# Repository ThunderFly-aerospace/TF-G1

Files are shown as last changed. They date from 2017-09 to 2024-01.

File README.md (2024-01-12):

# TF-G1 - Unmanned Autogyro Extreme weather sensor carrier  

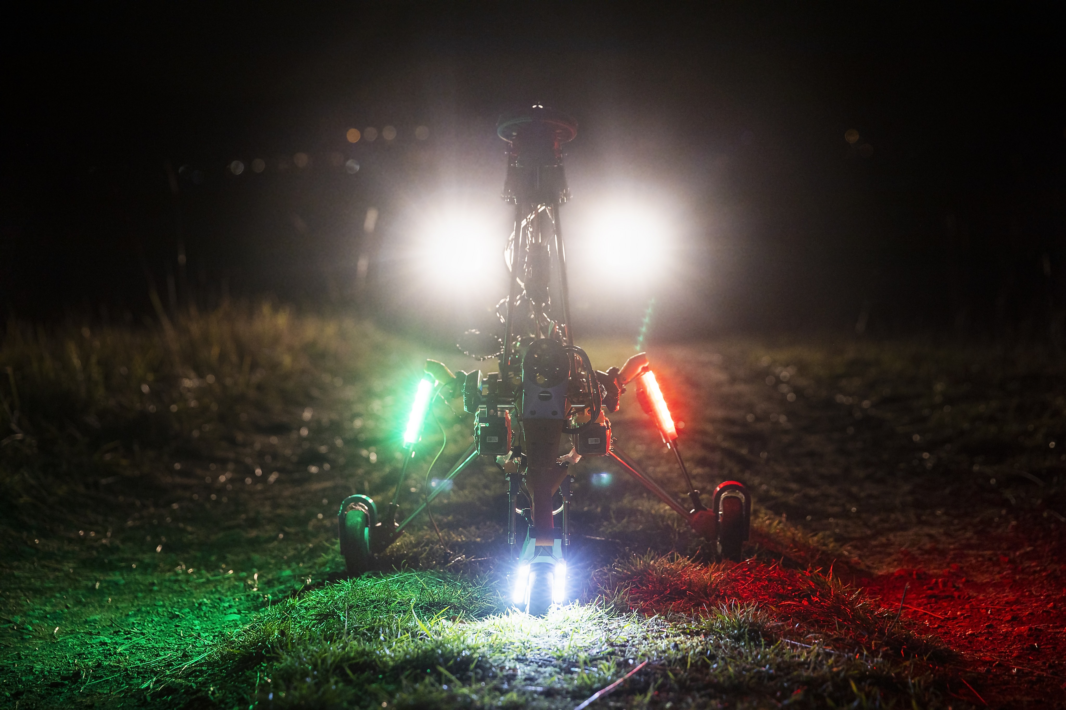
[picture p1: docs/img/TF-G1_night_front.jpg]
TF-G1 front view in night


The TF-G1 autogyro created by ThunderFly s.r.o. is a [unmanned aerial vehicle (UAV)](https://en.wikipedia.org/wiki/Unmanned_aerial_vehicle) designed to be operable in almost any weather.
The main features of that design are:

  * Payload capacity of a few kilograms
  * Weather-insensitive operation
  * Low audible noise
  * High safety due to stable autorotation mode which does not require autopilot or pilot attention
  * Greater altitude and area coverage than existing UAV designs  like multi-copters or helicopters
  * High maneuverability and agility
  * Absence of [downwash](https://en.wikipedia.org/wiki/Downwash), therefore a minimal occurrence of [Brownout](https://en.wikipedia.org/wiki/Brownout_(aeronautics))
  * High descent rates
  * [Simulation model available](https://github.com/ThunderFly-aerospace/FlightGear-TF-G1)
  * Easily repairable and maintain
  * Exceptional flight tolerance to rotor blade damage
  * Car roof takeoff ready

The benefits that come from this feature set are the usability of applications where the system could be potentially damaged, although the safety must remain as high as possible.  An example of this application is searching and rescue missions in harsh weather unflyable by conventional aircraft. For additional information contact ThunderFly s.r.o. representative at info@thunderfly.cz

## Why autogyro? 

Autogyro

In contrast to the well-known [VTOL](https://en.wikipedia.org/wiki/VTOL) aircraft designs. The autogyro could be considered a short take-off and vertical landing aircraft ([STOVL](https://en.wikipedia.org/wiki/STOVL)). Therefore it is suitable for a wide range of different applications. The main advantages to other well-known airframes: 

* Ability to take off and land using a short runway (almost zero length).
* High resistance to weather conditions, especially gusts of wind or thermals.
* An unpowered rotor enables it to operate in an autorotation mode (one of the helicopter’s emergency modes). Consequently, it does not need to actively change a flight mode in case of failure (it does not need a parachute or other actively working devices). Its flight is thus inherently stable and safe at all times.
* Autogyro has significantly reduced audible noise due to the slowly rotating rotor and propeller. 
* Absence of a downwash - during take-off or landing the creation of an unwanted swirling of dust is eliminated.
* Low lift-to-drag ratio that can be adjusted by construction parameters. This ability can be useful because an unmanned autogyro cannot fly very far in the case of control failure (as is the case of a conventional airplane), the flight is still safe and the autogyro cannot fall (as is typical for multi-copters or wrongly piloted helicopters).

The autogyro has generally many construction variants. The one, which is in the scope of this repository has a fully tilted rotor. The main advantage of this construction feature is obtaining better controllability over its wide airspeed range. It can also be controlled down to zero forward airspeeds, compared to a classical rudder/elevator setup.

## Repository content

This repository contains open-source design files of the autogyro construction. Most components are 3D-printed. However, the printable data (gcodes) are generated by our special software suite - processor3D. It is required that parts are sliced properly according to the material to make sure that resulted in 3D-printed parts can be used safely for the flight. **Therefore for safety reasons we do not recommend attempting to slice the parts yourself. It is better to contact us.**

The product, support, or accessories could be obtained from [ThunderFly s.r.o.](https://www.thunderfly.cz/), via an email to info@thunderfly.cz . 

### Contribution

In case you want to contribute to the open-source project we have a [contribution guideline](https://github.com/ThunderFly-aerospace/TF-G2/blob/4s/CONTRIBUTING.md). Your contribution is very welcome! For a contribution, you can get access to the optimized and safe printable files (gcodes).

##### Build

Most of the components are coded in OpenSCAD. To render all components run the following commands in Linux CLI:

    sudo pip install stlsort

    sudo apt install python3-numpy-stl

    make

The design files and related documents are covered by [GNU GENERAL PUBLIC LICENSE Version 3](https://www.gnu.org/licenses/gpl-3.0.en.html)

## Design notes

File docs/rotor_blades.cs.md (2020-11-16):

## Rotorové listy pro vírník TF-G1

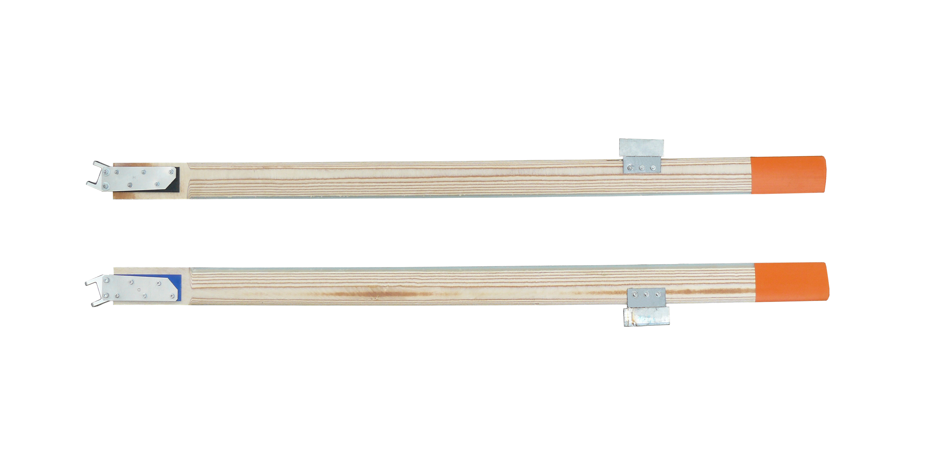
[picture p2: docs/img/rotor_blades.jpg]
Pár rotorových listů pro TF-G1


Rotorové listy vírníku TF-G1 jsou vícevrstvé z dřevo-skelného kompozitu. Každý list je pečlivě CNC frézován ve dvojici s druhým rotorovým listem pro udržení  precizního vyvážení každého rotorového páru.

Konstrukce listu je založena na sendvičové konstrukci, kde vnitřní stringer je dimenzován pro maximální únosnost 4kN, což odpovídá maximálním otáčkám 1500 ot/minutu.  Všechny vrstvy sendviče jsou vakuově lisovány pro eliminaci vzniku bublinek ve vnitřních lepených spojích.
Listy jsou vytvrzeny v autoklávu a povrchově ošetřeny epoxidovým lakem.

Závěs rotorového listu je navržen pro využití na Delta-3 rotorové hlavě s kluznými ložisky a broušeným ocelovým čepem 4H9.

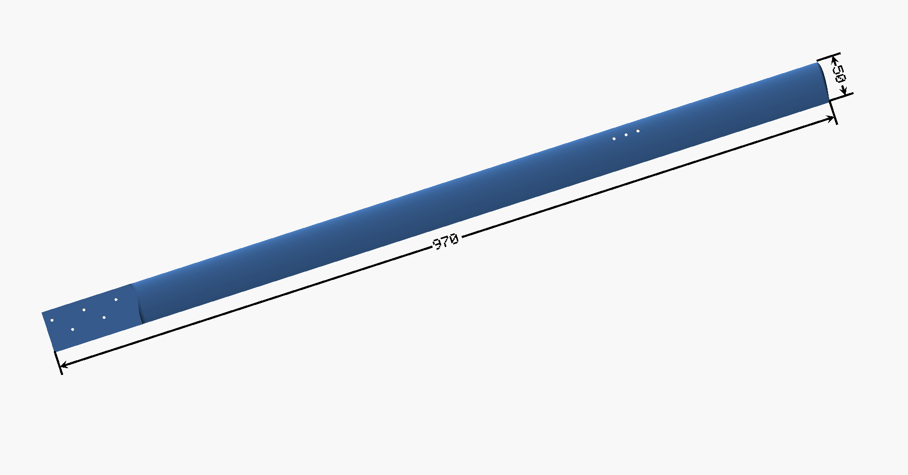
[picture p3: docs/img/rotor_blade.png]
TF-G1 samostatný rotorový list


Hlavní parametry rotorových listů

  - Aerodynamický profil NACA0016
  - Aerodynamické křížení: žádné
  - Průmět - obdélníkový
  - Hloubka listu 50mm
  - Délka 970mm
  - Maximální otáčky - 1500
  - Materiál: březový kompozit v kombinaci se skelnými vlákny FR4.
  - Hmotnost 564g
  - Typ kování: Pro Delta-3 rotorovou hlavu

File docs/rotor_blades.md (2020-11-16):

## TF-G1 Rotor Blades

Pair of TF-G1 rotor blades

TF-G1 rotor blades are multilayer wood-composite autogyro rotor blades.  The each blade is carefully CNC machined in tandem with the second rotor blade to maintain precise balance of each rotor pair.
The blade construction is based on wood-fiber-wood sendwitch, where internal stringer core is dimensioned to windstand 4kN centrifugal force corresponding to 1500 RPM.
Rotor blades has delta-3 rotor head mount.

TF-G1 plain rotor blade

Main blade parameters

  - Blade airfoil NACA0016
  - Shape - rectangle
  - Depth 50mm
  - Lenght 970mm
  - Maximal RPM - 1500
  - Material - birch plywood, glass fiber composite
  - Mass 564g
  - Blade mount type: Delta-3 rotor head

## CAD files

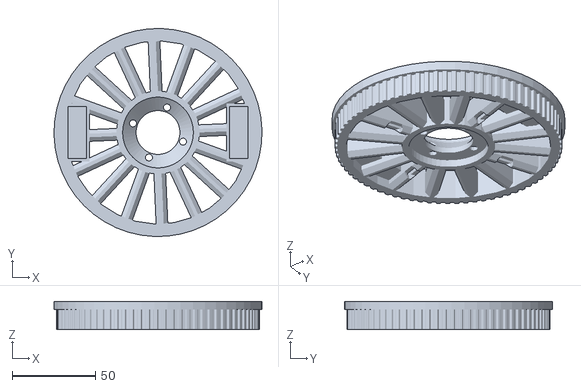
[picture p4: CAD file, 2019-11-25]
STL/drawings/assembly_head_rotor_printed.stl
125.0 x 124.9 x 17.0

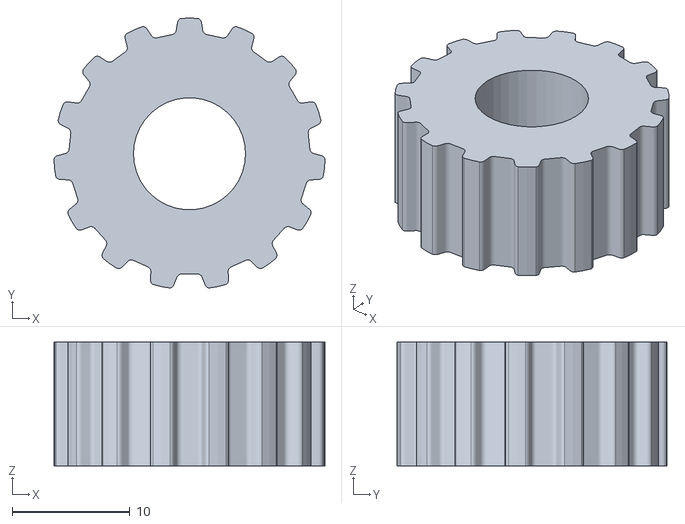
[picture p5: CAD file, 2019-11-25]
STL/drawings/assembly_printed_head_pulley_motor.stl
23.0 x 22.9 x 10.5

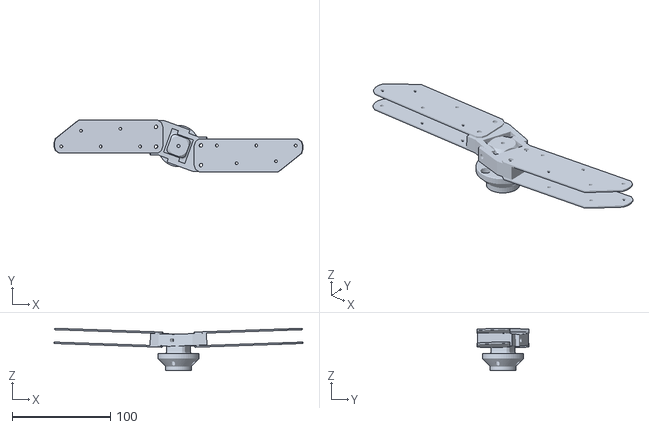
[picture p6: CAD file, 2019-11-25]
STL/drawings/assembly_head_rotor_alu.stl
252.9 x 52.3 x 43.1

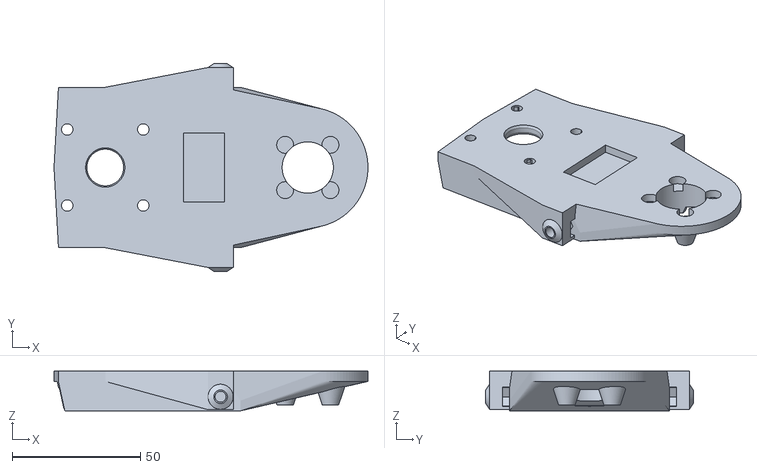
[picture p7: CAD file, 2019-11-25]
STL/drawings/assembly_head_plate_printed.stl
122.5 x 81.0 x 15.5

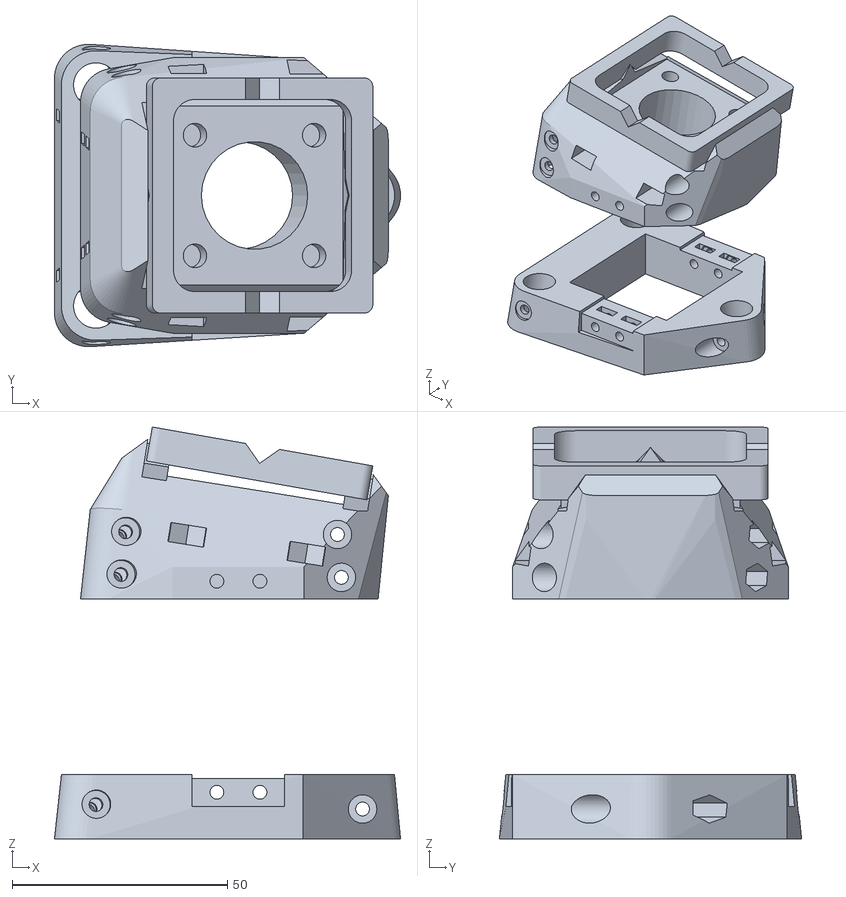
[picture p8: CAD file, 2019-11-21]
STL/drawings/assembly_printed_head.stl
80.4 x 70.2 x 95.7

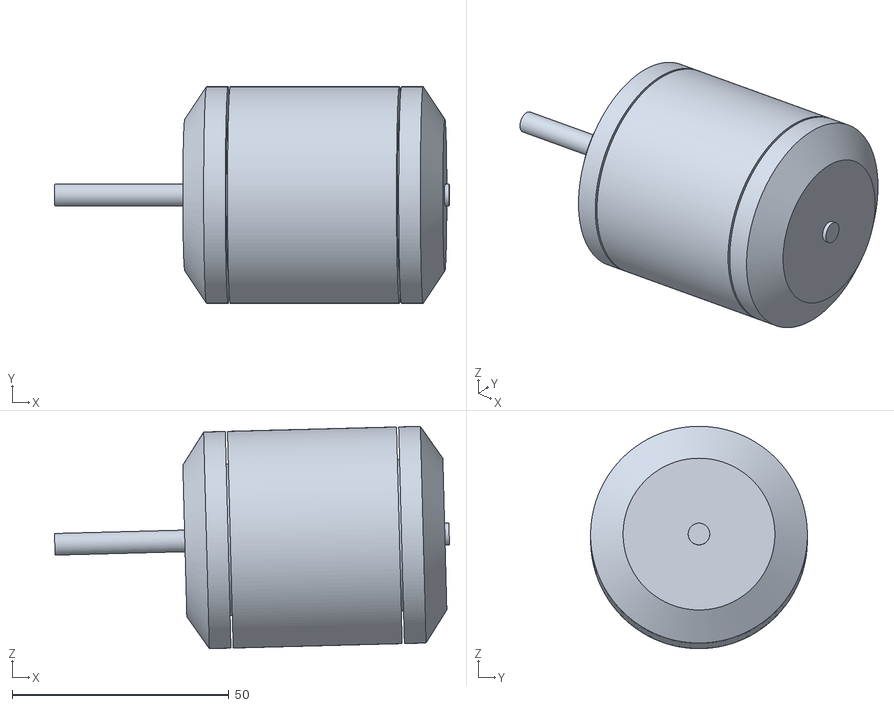
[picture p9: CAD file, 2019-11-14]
STL/main_motor.stl
91.1 x 50.0 x 51.3

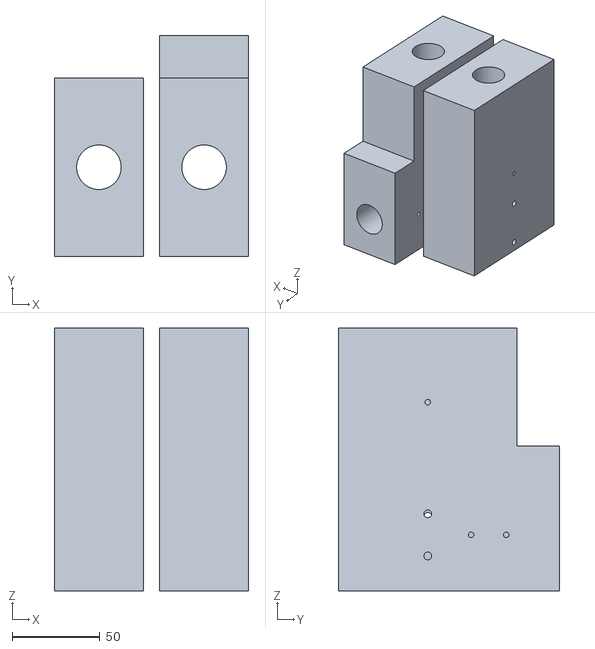
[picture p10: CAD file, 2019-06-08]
STL/manufacturing_helpers/print_plate_1014main_tube.stl
110.8 x 125.8 x 150.0

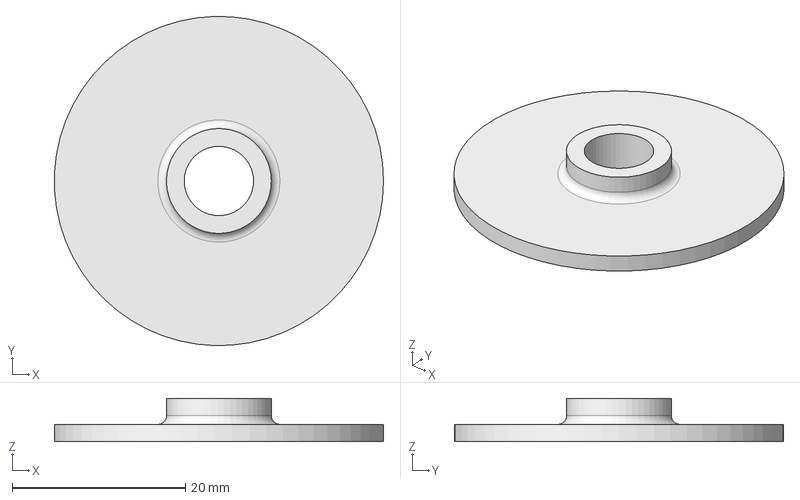
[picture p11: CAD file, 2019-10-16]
src/666_1264.FCStd
38.0 x 38.0 x 5.00 mm

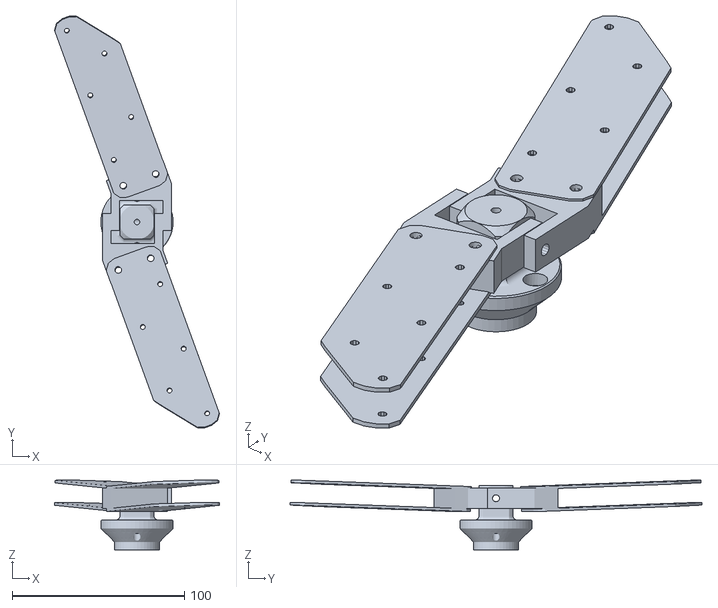
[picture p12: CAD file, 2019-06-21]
src/drawings/visual_model/rotor_hinges.stl
95.9 x 239.4 x 40.6

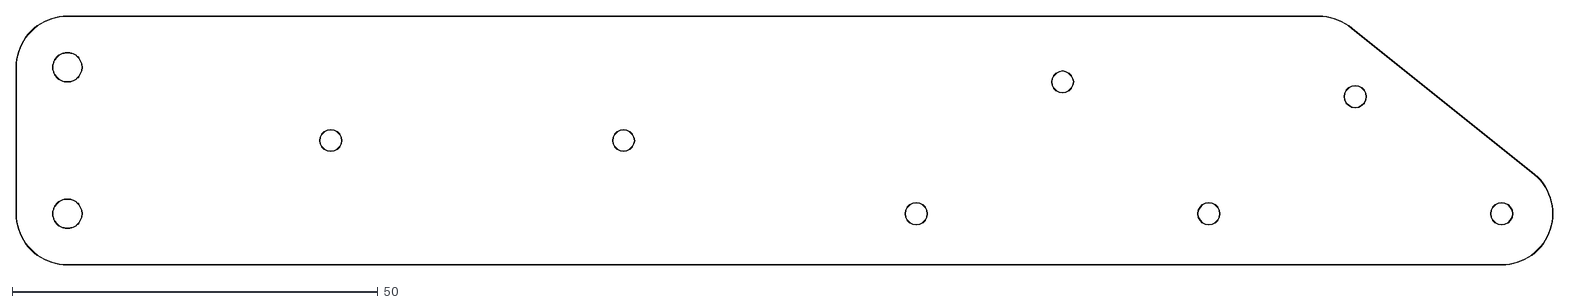
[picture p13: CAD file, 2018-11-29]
src/milling/DXF/666_1050_projection.dxf
210.0 x 34.0

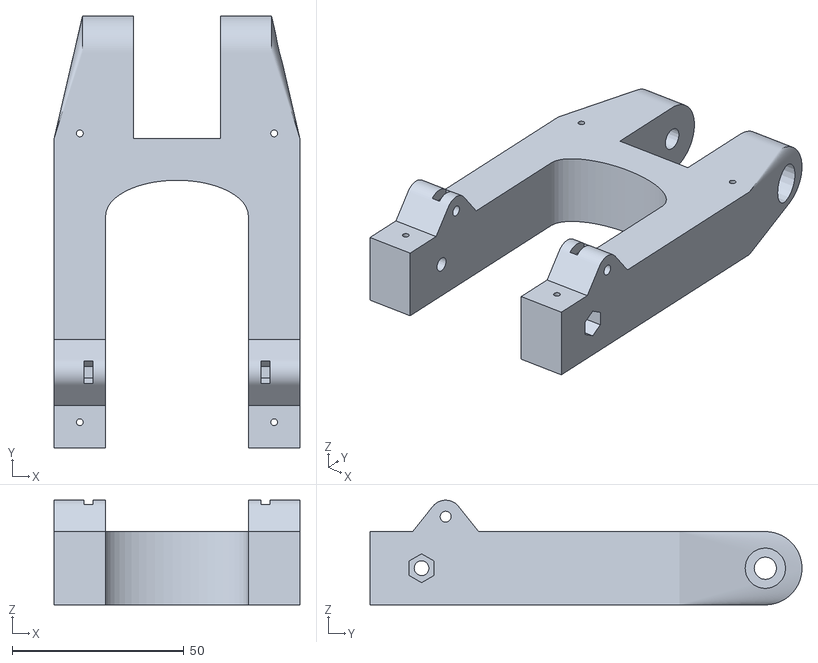
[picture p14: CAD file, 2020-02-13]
STL/888_2022.stl
71.5 x 125.7 x 30.5

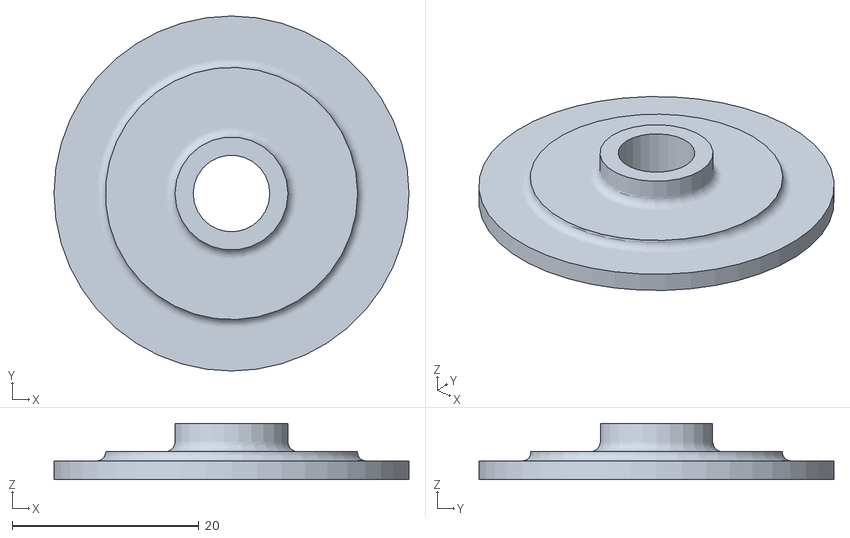
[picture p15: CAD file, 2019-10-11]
STL/manufacturing_helpers/666_1264_print.stl
38.0 x 38.0 x 6.00

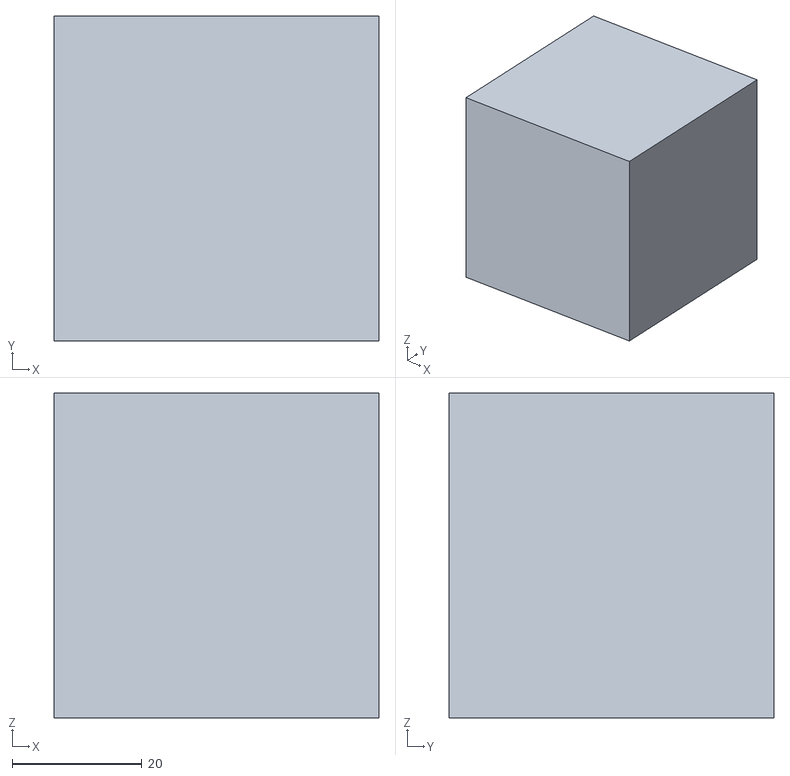
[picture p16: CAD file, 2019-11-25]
STL/testing/cube_center.stl
50.0 x 50.0 x 50.0

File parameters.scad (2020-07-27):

use <src/lib/vector.scad>

global_clearance = 0.5;
perimeter = 0.41;
layer = 0.2;
week = "77"; // Popisek s cislem tydne, nastavuje se z makefilu

// obecne rozmery trubek
carbon_pipe_10_outer_diameter = 10.4;
carbon_pipe_10_inner_diameter = 6;

//Main tube diameter - hole [mm]
main_tube_outer_diameter = 25.4;
main_tube_inner_diameter = 23.05;

//Tube for undercarriage - rendered hole [mm]
tube_for_undercarriage_outer_diameter = carbon_pipe_10_outer_diameter;
tube_for_undercarriage_inner_diameter = carbon_pipe_10_inner_diameter;

//Tube for pilon - rendered hole [mm]
pilon_pipe_diameter = carbon_pipe_10_outer_diameter;
pilon_pipe_diameter_inner = carbon_pipe_10_inner_diameter;


// Parametry hlavniho nosniku

beam_vertical_space_between_pipes = 1;
beam_min_wall = 3;
beam_socket_width = 25;

// tloustka limce
ring_thickness = 2*10 + beam_vertical_space_between_pipes + 3*beam_min_wall;

// tloustka podlozky, a tloustka podlozky od stredu smerem nahoru/dolu
beam_thickness = 2*10 + beam_vertical_space_between_pipes + 2*beam_min_wall;
beam_thickness_above = 5 + beam_min_wall;
beam_thickness_below = 5+ beam_vertical_space_between_pipes + 10 + beam_min_wall;
//beam_thickness = 30;
beam_width = 80;
beam_length = 490;
beam_edge_angle = 60/2;
beam_division = [0, 145, 275, 417, 1000];

beam_main_pipe_diameter = carbon_pipe_10_outer_diameter;
beam_main_pipe_distance = 45;
beam_main_pipe_thickness = carbon_pipe_10_outer_diameter;

beam_patern = 40;
beam_side_edge_width = 175;

// Parametry pro limec

collar_holes_distance = 200; // Vzdalenost der pro sesroubovani pricnych tyci. Vzdalenost na trubce
beam_side_pipe_distance = collar_holes_distance; // TODO: odstranit tento parametr


// Nastavení parametrů rotoru

gliding_aggle = 14;         // tenhle úhel by se zřejmě v budoucnu měl počítat z požadované klouzavosti.

rotor_blade_AOA = 3;      // nastavení úhlu náběhu rotorového listu
rotor_blade_length = 970;   // délka rotorového listu
rotor_blade_depth = 50;     // hloubka rotorového listu
rotor_flap0 = 2;
rotor_delta = 20;

/* // parametry rotorove hlavy

rotor_head_pitch = 0;
rotor_head_roll = 0;

rotor_head_height = 78; // vzdalenost spodni zakladny rotorove hlavy od stredu kuloveho loziska
rotor_head_width = 70; // je to "sirka" v ose X
rotor_head_rank_angle = 9; // zakloneni rotorove hlavy pri nulove vychylce.
rotor_head_bearing_x_shift = -0; // posun kuloveho loziska dopredu dozadu.
*/

rotor_head_plate_bearing_center_distance = 14;     // vzdalenost horni spodni steny placky od stredu loziska
rotor_head_limiter_above = 12; // jak moc vysoko ma byt divnotvar nad stredem loziska
rotor_head_limiter_below = 3; // jak moc nizko ma byt divnostvar pod stredem loziska

// nastavení parametrů motoru

engine_angle = -1.5;
engine_diameter = 55;
engine_offset = 65;
engine_holder_beam_depth = 50; // jak moc je nosnik zapusten v dilu

engine_screws_radius = 15;
engine_holes_radius = (24 + 44)/4;
engine_shatf_hole_diameter = 13;

// Parameters of tube couplings
coupling_wall_thickness = main_tube_outer_diameter/5;  //width of coupling walls
thickness_between_tubes = main_tube_outer_diameter/10;    // minimum distance between tubes in couplings

coupling_wall_thickness_undercarriage = tube_for_undercarriage_outer_diameter/3;
thickness_between_tubes_undercarriage = tube_for_undercarriage_outer_diameter/10;

608_bearing_outer_diameter = 22.3;
608_bearing_inner_diameter = 8-0.3+0.4;
608_bearing_thickness = 7.1;

696_bearing_outer_diameter = 15.3;
696_bearing_inner_diameter = 6-0.3+0.4;
696_bearing_thickness = 5.1;

//parametry mechoveho kola
wheel_inner_diameter = 36;
wheel_inner_thickness = 28;
wheel_outer_diameter = 108;

wheel_disc_diameter = 51;
wheel_disc_upper_thickness = 5;
wheel_disc_upper_difference = 7;

// screw length step - minimum difference in length between two types of screws
basic_screw_length = 5;

//Square nut for M6 [mm]
M6_square_nut_length = 10;
M6_square_nut_height = 3.2;

//Screw diameter and nut for M10 [mm]
M10_screw_diameter=10.4;
M10_head_height = 10;
M10_head_diameter = 16+0.5;
M10_nut_height = 10.5;
M10_nut_diameter = 25.5;
M10_nut_pocket = 22.3;

//Screw diameter for M8 [mm]
M8_screw_diameter = 8 + 0.5;
M8_head_height = 8;
M8_head_diameter = 13.5;
M8_nut_height = 7.5;
M8_nut_diameter = 14.4 + 0.5;
M8_nut_pocket = 13 + 0.5;

M8_plug_diameter = 8;

//Screw diameter and nut for M6 [mm]
M6_screw_diameter=6.5;
M6_head_diameter = 10+0.5;
M6_head_height = 6;
M6_nut_height = 4.9;
M6_nut_diameter = 11.8;
M6_nut_pocket = 10.4;

//Screw diameter and nut for M5 [mm]
M5_screw_diameter=5.5;
M5_head_height = 5;
M5_head_diameter = 13+0.5;
M5_nut_height = 4 + 0.5;
M5_nut_diameter = 9.4;
M5_nut_pocket = 8.4;

//Screw diameter and nut for M4 [mm]
M4_screw_diameter=4.3;
M4_screw_head_height = 4.5;
M4_nut_height = 3.2 + 0.5;
M4_nut_diameter = 8.4;
M4_nut_pocket = 7.5;

//Screw diameter and nut for M3 [mm]
M3_screw_diameter = 3.2;
M3_nut_height = 2.7;
M3_nut_diameter = 6.6;
M3_screw_head_height = 3;
M3_nut_pocket = 5.6;

//Screw diameter and nut for M2,5 [mm]
M2_5_screw_diameter = 2.7;
M2_5_nut_height = 2.3;
M2_5_nut_diameter = 6;
M2_5_nut_pocket = 5.1;

//Screw diameter and nut for M2 [mm]
M2_screw_diameter = 2.1;
M2_nut_height = 2;
M2_nut_diameter = 4.5;
M2_nut_pocket = 3.95;

//M3 ISO7380
M3_ISO7380_head_height = 1.5;
M3_ISO7380_nut_height = 3;
M3_ISO7380_nut_diameter = 5.7+0.5;

//sroub servo
Servo_screw = 1.5;
Servo_nut_height = 1;
Servo_nut_diameter = 2.7;

//The tube for help
Help_main_tube_outer = 25;
Help_main_tube_inner = 23;
Help_tube_for_undercarriage_outer = 10;
Help_tube_for_undercarriage_inner = 5;


//main hull parameters

hull_drop_length = 720;  // zajím sjednoceno s hull_x_size, ale v budoucnu by tento parametr chtělo zrušit
hull_wall_thickness = 0.8;
hull_y_size = 150;
hull_z_size = 230;
hull_x_size = hull_drop_length;
hull_corner_radius = 4;
hull_airfoil_thickness= 0035;  // thickness of drop generating airfoil in percent of length.
hull_scale_x = 1;
hull_scale_y = 1.5;
hull_scale_z = 1.5;

hull_strenghtening_pipe_distance = 45;




// Parametry pylonu k rotorove hlave

main_pilon_position = 170+68+beam_patern;       // pozice rotorového pilonu měřená od přední části krytu

// vzdalenosti jsou pocitany od stredu rotoru
// vzdalenosti jednotlivych tyci u podlozky
//pilon_pipe_base_front_x = 30;
pilon_pipe_base_front_x = +engine_holder_beam_depth + main_pilon_position - beam_patern*6.75;
pilon_pipe_base_front_y = 55;
pilon_pipe_base_front_z = 0;

pilon_pipe_base_rear_x = -engine_holder_beam_depth + beam_patern*9.75 - main_pilon_position;
pilon_pipe_base_rear_z = beam_thickness_above;

// vzhalenosti jednotlivych tyci u rotorove hlavy
pilon_pipe_head_front_x = 20;
pilon_pipe_head_front_y = 20;
pilon_pipe_head_rear_x = 30;

cover_pilon_position = main_pilon_position - 42;
cover_pilon_naca = 0060;
height_of_vertical_tube = 350; //278mm je změřená délka trubky.



//délka hlavní dlouhé trubky
length_of_main_tube = 820;
length_of_undercarriage_tube_front = 150;
length_of_undercarriage_tube_rear = 320; //500;

ribbon_width = 5; // šířka vyztužovacích lemů.

// šířka otvoru v přední části kapoty pro držák motoru.
width_of_engine_holder = 83;

//Top Cover Division - dělení horního krytu pro tisk
top_cover_division = [0, 50, 150, 290, 435, 580, hull_x_size];
top_cover_strip_zposition = 0;
//Bottom Cover Division - dělení dolního krytu pro tisk
bottom_cover_division = [0,145,290,365, 470, hull_x_size];
bottom_cover_strip_zposition = -15;
// zkrácená část pro payload pro testovací tisk
//bottom_cover_division = [0,200,250,365, 470, hull_x_size];


rotor_height = height_of_vertical_tube + main_tube_outer_diameter/2 + 2*global_clearance + thickness_between_tubes + 30; // změřená výška rotoru je 367mm
center_of_gravity_position = [main_pilon_position - tan(gliding_aggle)*rotor_height, 0, 0];


//Cover pilon division - na výšku (v ose Z)
cover_pilon_division = [0,170,height_of_vertical_tube + main_tube_outer_diameter + coupling_wall_thickness];
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

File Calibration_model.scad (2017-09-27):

include <./Parameters.scad>
wall_thickness = main_tube_outer_diameter/5;
width = wall_thickness * 3 + main_tube_outer_diameter + main_tube_inner_diameter;
depth = main_tube_outer_diameter + wall_thickness * 2;
height = 20;
protrusion_height = 10;

difference () {

translate ([-(main_tube_outer_diameter/2+wall_thickness),-(main_tube_outer_diameter/2+wall_thickness),0])
cube ([width,depth,height]);

cylinder (h = height, r1 = main_tube_outer_diameter/2, r2 = main_tube_outer_diameter/2);

translate ([-main_tube_outer_diameter/2,-main_tube_outer_diameter/2,0])
cylinder (h = height, r1 = M4_screw_diameter/2, r2 = M4_screw_diameter/2);

translate ([main_tube_outer_diameter/2 + wall_thickness + main_tube_inner_diameter/2,-4,0])
cylinder (h = height, r1 = tube_for_undercarriage_outer_diameter/2, r2 = tube_for_undercarriage_outer_diameter/2);

}

union () {

	difference(){

	translate ([main_tube_outer_diameter/2 + wall_thickness + main_tube_inner_diameter/2,-4,-(protrusion_height)])
	cylinder (h = protrusion_height, r1 = main_tube_inner_diameter/2, r2 = main_tube_inner_diameter/2);

		translate ([main_tube_outer_diameter/2 + wall_thickness + main_tube_inner_diameter/2,-4,-protrusion_height])
		cylinder (h = protrusion_height, r1 = tube_for_undercarriage_outer_diameter/2, r2 = tube_for_undercarriage_outer_diameter/2);


}
}

union(){

	translate ([main_tube_outer_diameter/2 + wall_thickness/2+2,main_tube_outer_diameter/2 - 2,-protrusion_height])
	cylinder (h = protrusion_height, r1 = tube_for_undercarriage_inner_diameter, r2 = tube_for_undercarriage_inner_diameter);

}

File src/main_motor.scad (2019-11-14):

include <../parameters.scad>
use <lib/motor.scad>

module position_main_motor(){
		translate([-engine_offset*2.2, 0, engine_offset])
		rotate([0, 90+engine_angle, 0])
		children();
}

position_main_motor()
motor_main();

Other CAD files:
STL/assembly_head_plate_printed.stl
AMF/4printing/print_plate_888_1025B1.stl
AMF/888_1038.stl
STL/blades/printplate_888_4101_printtest.3mf
src/motor_imitation.scad
666 1017_promenne.scad
666_1004.scad
666_1004_promenne_final_1.scad
666_1014.scad
666_1017.scad
666_1019.scad
AMF/333_1037.amf
AMF/4printing/print_plate_1014.amf
AMF/4printing/print_plate_1014.stl
AMF/4printing/print_plate_1019A.amf
AMF/4printing/print_plate_1019A.stl
AMF/4printing/print_plate_1019B.amf
AMF/4printing/print_plate_1019B.stl
AMF/4printing/print_plate_1020.amf
AMF/4printing/print_plate_1020.stl
AMF/4printing/print_plate_1024A.amf
AMF/4printing/print_plate_1024A.stl
AMF/4printing/print_plate_1024B.amf
AMF/4printing/print_plate_1024B.stl
AMF/4printing/print_plate_1026_engine.amf
AMF/4printing/print_plate_1026_engine.stl
AMF/4printing/print_plate_1028_adapter.amf
AMF/4printing/print_plate_1028_adapter.stl
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

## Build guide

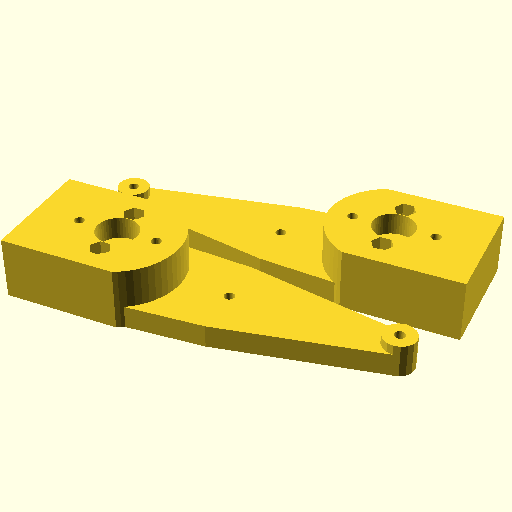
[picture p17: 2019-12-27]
images/4printing/print_plate_888_2021_arm.png

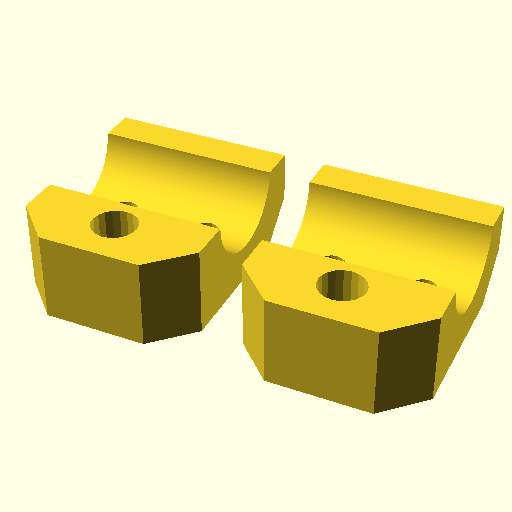
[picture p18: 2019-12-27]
images/4printing/print_plate_1014.png

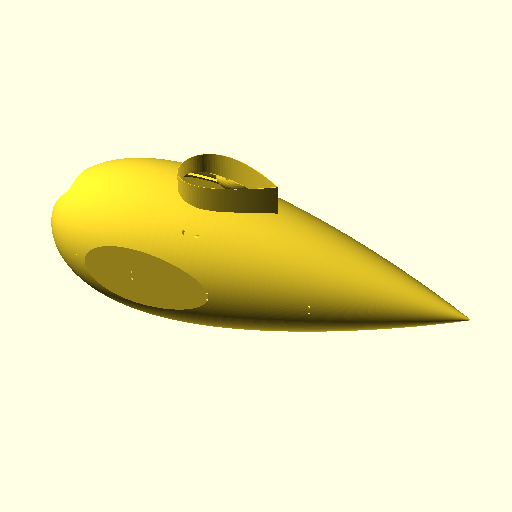
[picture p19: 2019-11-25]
images/drawings/assembly_cover.png

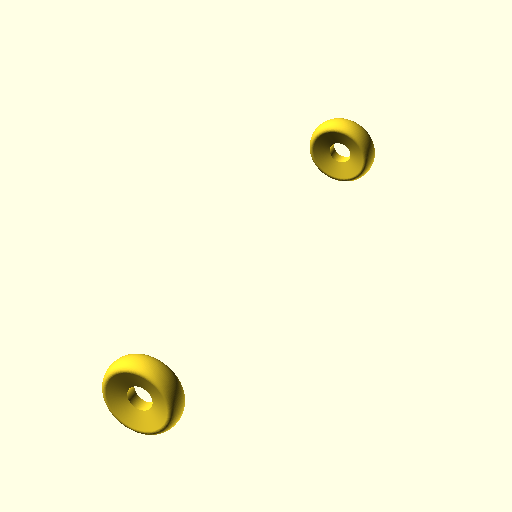
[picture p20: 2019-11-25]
images/drawings/assembly_chassis_wheel.png

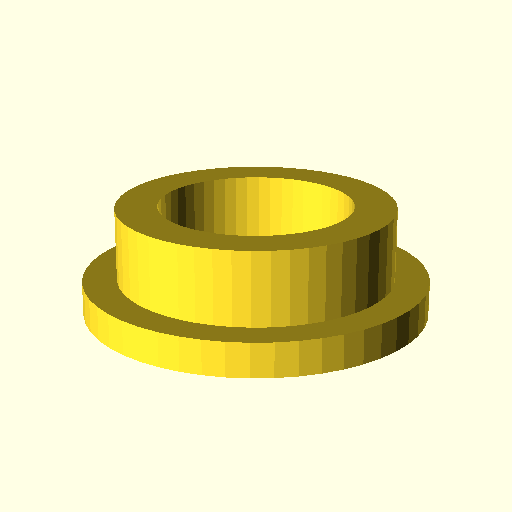
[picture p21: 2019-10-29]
images/4printing/print_plate_888_1023_3-2.png

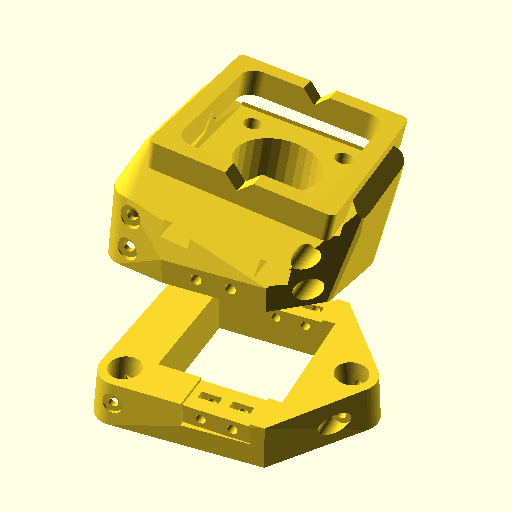
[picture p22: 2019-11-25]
images/drawings/assembly_printed_head.png

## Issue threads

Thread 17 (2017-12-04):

Kryt 666_1032 nepasuje na díl  666_1025

kaklik, 2017-12-04:
- Tolerance pro nasunutí dílu 666_1032 přes kryt 666_1025 je moc malá (minimálně o 1.5mm)

Elizaa62, 2017-12-04:
Já jsem tam ten nástavec na dílu 666_1025 už nějak zmenšovala, ale asi je to zmenšení stále malé..

Elizaa62, 2017-12-05:
Vytvořila jsem dva nové díly 666_1025ZK1 a 666_1025ZK2 určené jen pro rychlý tisk a následnou kontrolu držáku.

kaklik, 2017-12-05:
Zjistil jsem že po úpravě kryt pylonu stále nepasuje do držáku na horní části kapotáže.  Příčinou byla nesprávně zmenšená část pro držák.  Zmenšení o 2mm tak nebylo rezervou pro tolerance, ale prostým celkovým zmenšením.  Upravil jsem proto zdrojový kód tak, aby držák zmenšoval správně a navíc jsem zavedl proměnnou "clearance", která umožňuje nastavit velikost tolerančního prostoru mezi díly.
K tomu bylo potřeba pracovat s úhlem odtokové hrany a délku profilu zmenšit patřičně k velikosti tohoto úhlu.

Closed 2017-12-07.

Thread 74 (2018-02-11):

Nastavení výšky krytu pylonu (díl 666_1032)

kaklik, 2018-02-11:
Líbilo by se mi, kdyby kryt pro pylon 666_1032 byl vyřešený tak, že se jeho výška dopočítá automaticky, z délky vertikální středové trubky (pylonu).

Pak by bylo možné uříznout definovaně dlouhou vertikální trubku a vytisknout kryt, který k ní bude pasovat.  Poměrně výrazně to pomůže pro jednodušší nastavení polohy těžiště.

Elizaa62, 2018-02-11:
Myslím si, že jsem to vyřešila.

Elizaa62, 2018-02-11:
Máš to i s komentem.

kaklik, 2018-02-13:
Zkoušel jsem to použít a je to skoro dobře :)

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

Akorát to myslím nezohledňuje výšku držáku krytu a kryt je tak přibližně o výšku držáku kratší.

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

Elizaa62, 2018-02-13:
Teď asi nerozumím, co mám přesně opravit..

kaklik, 2018-02-13:
Myslím, že k tomu může pomoc horní obrázek, který jsem sem přidal.  Je na něm vidět, že kryt pylonu má pod horní spojkou která se nasazuje na trubku vůli.  To je úplně v pořádku.
Ale zároveň pod krytem dole, je mezi kapkovitým horním krytem a krytem pylonu mezera. Což znamená, že když by se kryt pylonu nasadil na držák, který je na horním krytu kapky, tak jak bude reálně nasazený.  Tak kryt pylonu bude moc krátký.
Mezi spojkou na konci vertikální trubky a krytem pylonu vznikne myslim si až zbytečně velká mezera. Která tam jinak nemusí být skoro žádná, až na tolerance tisku.

Elizaa62, 2018-02-13:
Je mi divné, že mezi držákem na horním krytu a krytem pylonu je taková mezera. Myslela jsem, že výška toho držáku na horním krytu vůbec s ničím nesouvisí.

Elizaa62, 2018-02-13:
A dělal jsi to v té sestavě 888_1005?

kaklik, 2018-02-13:
Výška držáku na horním krytu je myslím doplněním do kvádru, kterým se ořezává kapka.   Konečná pozice krytu pylonu by měla myslím být taková, že bude nasazením přes držák doléhat až na horní stěnu horní kapky.
Dělal jsem to v sestavě 666_2000, ale to by mělo být jedno, protože ta výška krytu pylonu se skutečně mění a to je to, co jsem chtěl ověřit.

Elizaa62, 2018-02-14:
Výška vyřešena.

kaklik, 2018-02-16:
Ano, připadá mi, že to funguje.

kaklik, 2018-02-26:
Tak se mi zdá, že výpočet výšky krytu zanedbává posun vertikální trubky pylonu nad centrální trubku.
Podle mě je v modelu 1017 tahle vzdálenost tvořena součtem width/2 + (- global_clearance*2), chtělo by o věřit v nějaké celkové sestavě, že ta délka trubky je vážně vypočítána správně.

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

Přišel jsem na to tak, že v Parameters.scad mám délku trubky nastavenou asi o 3mm kratší, než je reálná změřená.  Kryt by tak měl mít vůli ty 3mm.  Reálně je ale přesně na těsno.

Elizaa62, 2018-02-27:
Délku vertikální trubky máš v Parameters nastavenou, tak jak jsi chtěl. Tzn. 195 mm. A tady o tom posunu jsem ti psala, že si nejsem jistá, že je to správně nastavené.

Ale pokusím se to dát nějak dohromady.

kaklik, 2018-02-27:
Udělal jsem pull-request, kde jsem to nastavení délky změnil.  Ono je to skoro dobře.  Jenom ten model krytu nepočítá s tím, že trubka pylonu je trochu výše, díky tomu, že nezačíná úplně přesně na stěně té horizontální trubky.

Elizaa62, 2018-02-27:
Výška dílu 666_1017 je konstantní, v kódu je nastaveno 70 mm. Mezeru mezi trubkami jsem nastavila na coupling_wall_thickness. Tím pádem si vytiskni díl 666_1017 znovu a už by to mělo sedět.

kaklik, 2018-02-27:
Dobře, ještě jsem to upravil tak, aby mezera mezi trubkami byla podle existující proměnné "thickness_between_tubes", která je pro tenhle rozměr myslím vhodnější.
Na to, abych to otestoval musím přetisknout jak spojku, tak kryt, takže se to dám do tiskového plánu.

Closed 2018-02-27.

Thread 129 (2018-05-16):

Otvory pro spojky trubek v podložce

kaklik, 2018-05-16:
Při skládání prvního kusu jsem narazil na komplikaci, že šrouby ve spojkách 666_1004 přesahují přes obrys spojky. Díky tomu podložka nešla nasadit na sešroubovanou kostru z trubek. Šrouby, které jsem použil byly DIN912 M3x35.
Zajímavé je, že přesahovaly symericky jak hlavičkou, tak i koncem šroubu přes matku. Vyřešil jsem to tak, že jsem do podložky pilníkem vypiloval drážky, v otvorech pro spojky.  Takže přesahující šrouby byly v drážce, podložka pak už šla na spojky nasadit.

U spojky 666_1017 byla situace jiná. Tam jsem sice použil stejné šrouby, ale výsledek byl takový, že hlava šroubu zapadla přesně do šestihranného zapuštění tak, že nepřečnívala přes povrch. Šroub ale v důsledku toho více přečníval na druhé straně za matkou. Tady jsem to vyřešil tak, že jsem šroub ubrousil na délku, která je zároveň s matkou.

Správné řešení celé situace zřejmě je:

- [x] Sjednotit hloubku šestihranného zapuštění na všech spojkách tak, aby do něj vždy zapadla celá hlavička šroubu.
- [x] Vymyslet, jak by šlo zajistit, aby do spojek pasovaly šrouby v délkách, které se vyrábí.

kaklik, 2018-05-16:
Ty délky šroubů by zřejmě šlo vyřešit tak, že se podle vypočteného rozměru spojky (Tak jak to funguje teď) odhadne nejbližší násobek 5ti.
Šrouby se v těchto délkách vyrábí s odstupem 5mm viz: https://www.valentazt.cz/imbusove-srouby.html

Elizaa62, 2018-05-18:
K bodu 1: Zapuštění jsem u spojek zkontrolovala a nikde problém nevidím. Dle mého názoru je problém v tom, zda sis zkontroloval výšku hlavičky šroubu s hodnotou, která je v Parameters.scad. Hodnota Nut_height_M3 musí být větší než hodnota výšky hlavičky šroubu. Pokud není, tak je jasné, že hlavička bude přečnívat.

kaklik, 2018-05-18:
Takže myslíš, že je možné, že bych měl vytištěné různé díly v různých verzích s různým nastavením výšky Nut_height_M3 ? No asi se to stát mohlo, v tom případě bude u nových dílů hlavička zapuštěná celá a bude přečnívat šroub na druhé straně, jak se to stalo u spojky pro vertikální trubku, která byla tištěná jako poslední.

Elizaa62, 2018-05-21:
To je možné, protože vím, že už jsem jednou kontrolovala zapuštění tak aby bylo všude stejné. Tak je pravděpodobné, že máš vytištěné ještě staré verze. Protože teď při kontrole nebylo k opravě skoro nic.

A musí se zkontrolovat výška Nut_height_M3, protože jak koukám na ten odkaz https://www.valentazt.cz/imbusove-srouby.html, tak hodnota "k", což je výška hlavičky šroubu, je u šroubu M3 3 mm a my máme v Parameters.scad pro Nut_height_M3 hodnotu 2,7 mm. Takže i kdybys teď vytiskl novou spojku, tak hlavička bude přečnívat u M3 o 0,3 mm.

kaklik, 2018-05-21:
Tady je zřejmě asi ještě rozdíl v tom, že hlavička a matka má vlastně jinou výšku, ale to není potřeba řešit, protože ty 0.3mm se ztratí. Ten díl se totiž při dotažení šroubu poměrně výrazně zdeformuje, takže hlavička reálně nepřečnívá.
Na straně matky je to ale opačně, tam naopak s větším dotažením šroub více vyčnívá. Což znamená že díl musí být zřejmě o nějakou malou toleranci širší, než je celková délka šroubu.

Elizaa62, 2018-05-22:
K té délce šroubů. Délka šroubu se skládá z délky šroubu + výšky hlavičky. Pro ilustraci na spojce 666_1004. Šířka této spojky je main_tube_outer_diameter + 2*coupling_wall_thickness = 25,4 + 2*(25,4/5) = 35,56.

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

Tento obrázek znázorňuje rozměry na šroubu.

Pro spojku 666_1004, která je široká 35,56 mm, potřebuješ šroub o délce 32,56. Protože musíš od šířky odečíst výšku hlavičky 3 mm pro M3, která má být ve spojce zapuštěná. Zde bude zapotřebí šroub M3x35 a šířka spojky se bude muset zvětšit tak, aby byla 35+3 = 38 mm. Když budeš chtít použít šroub M3x30, tak se spojka bude muset zmenšit na 30+3 = 33 mm.

U dalších spojek budou samozřejmě rozměry nejspíš jiné. Ilustrovala jsem to jenom na této.

Tak navrhni, jak to mám změnit. Protože v případě, že se bude muset měnit šířka spojek kvůli šroubům, tak to znamená změny i v ostatních modelech.

Elizaa62, 2018-05-23:
Podle tvého návrhu jsem opravila spojky 666_1004, 666_1017 a 666_1026. Přičemž u prvních dvou spojek je šířka včetně výšky hlavičky šroubu. Otvory pro hlavičky šroubů a pro matku jsou sjednoceny stejnou výškou "Screw_head_height_M3".

U třetí spojky je hlavička šroubu i matka mimo spojku, tudíž pro šířku matky jsem použila výpočet normalizované délky šroubu od které jsem odečetla výšku hlavičky šroubu "Screw_head_height_M4", aby šroub přečníval a bylo na něj možné nasadit matičku.

kaklik, 2018-05-23:
Paráda, podívám se na to. :)

kaklik, 2018-05-23:
Tak myslím, že to funguje dobře. Mám radost, že jsi to zvládla vyřešit. :)

Myslíš, že je lepší ty rozměry počítat takhle pokaždé znova? Já si právě říkal, že by možná bylo lepší, ten výpočet provést rovnou v tom společném souboru parameters.scad.  Aby si to každý model nemusel počítat samostatně.

Ta spojka 666_1026 je pro tenhle výpočet problematická, protože je právě jiná tím, že se  šroub nezapouští. Ale jsou na něm ještě plechy a podložky a jsou to díly, které nejsou nakreslené v openscadu, takže jejich rozměry se zatím nedají automaticky měnit. To se ale doufám jednou stane. Takže ten výpočet tam zatím nech. Jenom by teď bylo potřeba, aby  dočasně dával konstantní šířku spojky 666_1026  **50mm**.  To můžeš udělat například tím, že odečteš ještě vhodnou tloušťku plechů, aby to vyšlo.

Elizaa62, 2018-06-05:
Už asi vím, kde vznikl problém s pozici zadní spojky. Jak se měnila šířka spojky tak, aby pasovala na normalizované šrouby, tak jsem změnila i parametr "second_undercarriage_hole" podle, kterého se zadní spojka umisťuje.

Původně se počítal jako:
second_undercarriage_hole = main_tube_outer_diameter*2 + 2*coupling_wall_thickness + main_tube_outer_diameter + 170 + 160;

a teď se počítá:
second_undercarriage_hole = main_tube_outer_diameter*2 + coupling_width_666_1004 + 170 + 160;

Změnou je šířka spojky ->místo "main_tube_outer_diameter + 2*coupling_wall_thicknes" je zde "coupling_width_666_1004", která je samozřejmě větší.

Proto nejspíš došlo k jinému umístění zadní spojky. Jinak si to nedovedu vysvětlit.
Takže to nejspíš asi mám opravit na to původní počítaní, že?

Jinak ještě k těm šířkám spojek dle normalizovaných šroubů.. Šířku spojky 666_1026 jsem udělala konstantní 50 mm, jak jsi psal výše. Použila jsem k tomu nový parametr "thickness_of_plate", který se počítá jako nová šířka spojky mínus konstantní šířka 50mm a tento parametr se pak odečte od normalizované šířky, abychom dostali konstantní šířku 50 mm.

kaklik, 2018-06-06:
Aha :) To je fajn, že jsi na to přišla.

Přemýšlím, jak by to mělo fungovat správně a myslím si, že ve skutečnosti by pozice těch dvou spojek (přední a zadní) měla být nějak dána délkou hlavní trubky.  Protože délka kapky a vůbec všeho bude potřeba větší s rostoucí délkou hlavní trubky.

Navrhoval bych ale zatím to neměnit, dokud nedokončíme zkoušky s již vytištěnou podložkou. Tu posunutou díru jsem totiž využil na to, že jsem tudy protáhl kabely k servům na ocasních plochách.

Takže nejvíc by mi teď asi pomohlo ten zadní otvor zvětšit o polovinu jeho současného rozměru směrem dopředu. Abych tam příště až tu podložku budu tisknout nemusel řezat pilkou.

S tou spojkou 666_1026 jsi to vymyslela hodně dobře. :)

kaklik, 2018-06-19:
Ten otvor pro zadní spojku by zřejmě chtělo upravit tak, aby za ním zůstalo místo pro kabelové prostupy do podélné trubky. Viz fotka:

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

Elizaa62, 2018-06-26:
Změnila jsem parametr "second_undercarriage_hole" na původní výpočet, aby v tom nebyly další zmatky. Otvor jsem zvětšila o coupling_width_666_1004/2 a posunula o tuto hodnotu dopředu. Ten otvor na kabely tedy bude tedy velký coupling_width_666_1004/2 nebo chceš, aby byl velký jako uvádíš na obrázku?

Elizaa62, 2018-06-26:
Dobře :)

kaklik, 2018-07-19:
Tak jsem zjistil, že výpočet pozice zadní spojky ve skutečnosti nebyl navrácen na původní. Protože ta pozice zadní spojky je ve skutečnosti rozbitá mnohem déle.  A to konkrétně od tohoto commitu:
https://github.com/Elizaa62/Components/commit/02fbde8e85179fd5ff120c0bf4c55bff340a4926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

Přišel jsem na to tak, že když jsem si zobrazil tenhle náhled:

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

Kde je vidět, že spojka je moc vzadu.

Nyní jsem to myslím opravil tak, že jsem tam nastavil pozici před commitem, kde se to rozbilo.
Zároveň jsem zavedl novou díru jenom pro kabely od serv na ocasu, kterou jsem posunul mezi vertikální trubku a zadní spojku.

Takže teď to vypadá takhle:

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

kaklik, 2018-07-24:
Po tom co jsem do nové trubky vyvrtal otvory podle vrtacího přípravku 888_1014.scad jsem zjistil, že pasují všechny díry až na úplně přední díru pro šroub, který drží podložku na hlavní trubce.
Díra je přibližně o polovinu průměru posunutá více dopředu, než by měla být.  Takže skrz podložku do ní nelze prostrčit šroub.

Když jsem se pokusil jenom rychle zjistit, čím by to mohlo být, tak to vypadá, že je i nějak posunutá přední spojka pro podvozkovou trubku.

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

Zřejmě se tedy otvory posouvají do pozic které jsou různé v přípravku a na podložce.

Tomu odpovídá i to, že otvor je v podložce umístěný podle:
https://github.com/kaklik/Components/blob/4a4389497d42c02da4d14f9e1848017d990a3da6/src/666_1027.scad#L538

Ale v přípravku je umístění nastaveno jako:
https://github.com/kaklik/Components/blob/4a4389497d42c02da4d14f9e1848017d990a3da6/src/manufacturing_helpers/888_1014.scad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

Elizaa62, 2018-09-17:
Chyby plynou ze změněné šířky spojky 666_1004, jelikož se rozměry spojky mění podle délky šroubu. Všechny následující parametry pro umístění dalších spojek a dalších souvisejících komponent jsou uvedeny s pevnými parametry pro spojení. Pokusím se to opravit, ale změny se projeví ve více souborech.

Změny:
-> Parametr "second_undercarriage_hole" na height_1026 + height_1004/2 + 170  + 160. Musí se projevit změna šířky spojky 666_1004. Tudíž se mění pozice všech komponent závislých na parametru "second_undercarriage_hole" (otvory pro spojky v 666_1027, pozice podvozkových trubek)

-> pozice samotné spojky 666_1004, která je nyní height_666_1026 + height_1004/2.

-> 888_1008 - počátek podvozkových trubek je v ose x v height_666_1026 + height_1004/2.

kaklik, 2018-09-17:
Asi to způsobí komplikace, protože budu muset přetisknout hodně dílů a udělat v podstatě nový kus. Zřejmě to ale potřeba opravit, aby se nám ten model nerozbíjel při změně souvisejících parametrů.

Elizaa62, 2018-09-17:
Musela jsem to opravit, protože je zdlouhavé pořád přemýšlet nad tím, jak to je.

kaklik, 2018-09-17:
Ne, já to tak právě chci. Je správně, že jsi to opravila. :)

kaklik, 2018-09-25:
Ty spojky jsou zřejmě už správně.
Zůstala ale nějaká divnost v pozicích příčných podvozkových trubek vůči spojkám.
Je to vidět na tomto obrázku:

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

Elizaa62, 2018-11-20:
Koukala jsem na model 666_2000 a žádný problém v pozici jsem neshledala..

kaklik, 2018-11-29:
Budeme používat sestavu, která obsahuje méně chyb, tedy 666_2000.  Druhá sestava se může smazat.

Elizaa62, 2019-02-02:
Jsou v tomto issue nějaké záležitosti, které potřebují vyřešit?

kaklik, 2019-02-02:
Viděl jsem že druhá sestava je smazaná, takže je to zřejmě vyřešené.

Closed 2019-02-02.

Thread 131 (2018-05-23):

Úprava držáku motoru 666_1038 pro výkonnější motory

kaklik, 2018-05-23:
Nový výkonnější motor má jinou rozteč montážních otvorů na čele motoru.   Původní motor [C3548-900](https://www.rc-zoom.cz/ray-g2-stridavy-motor-c3548-900/) měl montážní otvory M3  v čele umístěné na kružnici s průměrem 25 mm. Nový motor  [C4120-750](http://www.pelikandaniel.com/?sec=product&id=72873) má montážní otvory pro šrouby M4 umístěné na kružnici s průměrem 30 mm.

Původní výkres držáku motoru se jmenuje 666_1038.dxf

Zároveň se zvětšil průměr motoru z 35 mm  na 49.5 mm. Délka zůstala téměř zachována 48 na 49 mm.

kaklik, 2018-05-27:
Přidána navá verze plechu držáku většího motoru. Během následujícího týdne se díl pokusím vyfrézovat.
https://github.com/kaklik/Components/blob/master/src/milling/666_1038.dxf

kaklik, 2018-05-30:
Držák dílu jsem rozšířil  a pojmenoval ho jako 888_1026.

Closed 2018-05-30.

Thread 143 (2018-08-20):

Nabíječ Raytronic C15 přebíjí akumulátory

kaklik, 2018-08-20:
Dva akumulátory http://www.pkmodelar.cz/akumulatory-lipol-akumulatory-letecke-4-clanek-lipol/foxy-g2-li-pol-5000mah-14-8v-40-80c-74-0wh-3eb4038
Se nám začaly nafukovat. Je to pravděpodobně tím, že  nabíječ překračuje maximální nabíjecí napětí akumulátoru a místo koncového vybíjecího napětí 16,8V nabíjí akumulátory až na 17V.

Řešení zřejmě je nějak upravit konfiguraci nabíječe.

kaklik, 2018-09-08:
Snížil jsem nastavení konečného nabíjecího napětí z 4.20 V na 4.18 V. Menší hodnotu nelze nastavit.

Closed 2018-09-08.

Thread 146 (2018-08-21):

Držák pro start ze střechy automobilu

kaklik, 2018-08-21:
Pro start vírníku bude potřeba mechanismus který umožní start ze střechy automobilu.   Pro základní experimenty je nutné, aby konstrukce byla především bezpečná.
Takže bude realizovaná tak, že na příčníky bude našroubovaná deska z voděodolné překližky o rozměrech 250x125cm tlustá 15mm.

Na tuto desku bude teprve našroubovaný vypouštěcí mechanismus, tak že v desce budou narážecí matice M10 do dřeva. Do kterých se z druhé strany našroubují šrouby.
Samotný vypouštěcí mechanismus může být realizovaný z hliníkových profilů a tištěných dílů.
Odjištění vírníku během vypouštění lze předpokládat [přídržným elektromagnetem s permanentním magnetem](https://www.magnety.cz/pridrzne-elektromagnety/pridrzne-elektromagnety-s-permanentnim-magnetem/).

Elektromagnet, jako těžší komponenta by zřejmě měl zůstat na vypouštěcím automobilu a kotva zůstane na podvozku vírníku.

Uchycení vírníku před opuštěním držáku musí splňovat tyto parametry

- Volnost pohybu v ose pitch alespoň 0 až +20 stupňů
- Volnost pohybu v ose yaw maximálně +/-5 stupňů
- Volnost pohybu v ose Roll +/- 15 stupňů.
- Nemožnost vyskočení z držáku vibracemi a nárazy při rozjezdu
- Nemožnost vypadnutí z držáku při prudkém zabrždění automobilu v jakékoliv fázi startu až do odjištění.

Konvence pojmenování os je patrná z [tohoto obrázku](https://upload.wikimedia.org/wikipedia/commons/c/c1/Yaw_Axis_Corrected.svg).

Uchycení proto zřejmě bude realizované [kardanovo spojkou](https://en.wikipedia.org/wiki/Universal_joint) na jejímž volném konci bude magnet držící podvozek UAV.  Spojka ale musí omezovat zosah volností podle seznamu výše. Konstrukčně lze vyjít například z [tohoto návrhu](https://www.thingiverse.com/thing:392828/files). Použití kuličkových ložisek pro uvažovanou aplikaci ale není nutné.

Postup vypouštění bude následující.

1. Aktivace avionických systému UAV a kontrola vypouštěcího mechanismu.
2. Postupný rozjed automobilu na max 50km/h.
3. Růst otáček rotoru
4. Zvednutí přídě UAV na doraz vypouštěcího mechanismu, díky dostatečnému vztlaku rotoru.
5. Autopilot vyrovná náklony v osách Roll a Yaw a stabilizuje osu Pitch, tak aby nebylo dosaženo žádného dorazu vypouštěcího mechanismu
6. Odjištění vypouštěcího mechanismu a přechod do stoupání směrem před automobil. (Automobil se vzdaluje za vírník) a vírník opouští vypouštěcí mechanismus v kvadrantu 0-90stupňů měřeno od přídě automobilu.

 Z toho je zřejmé, že je potřeba, aby došlo ke koordinaci mezi UAV, člověkem který jej pilotuje a vypouštěcím zařízením na střeše automobilu. Vhodným technickým řešením takového úkolu zřejmě může být použití [ROS](http://www.ros.org/), který na základě dat přijatých přes MAVlink odjestí vypouštěcí mechanismus.
Pro odjištění ale musí dojít ke shodě z těchto míst:

1. Pilot UAV musí dát signál k vypuštění
2. Autopilot UAV musí měřit parametry vhodné k vypuštění
3. ROS systém v automobilu musí telemetrické parametry vyhodnotit jako odpovídající požadavku na vypuštění
4. operátor automobilu nesmí mít zapnuté blokování vypouštění. (Přepínač odpojující elektrický okruh vypouštěcího elektromagnetu)

roman-dvorak, 2018-09-11:
Vypouštěcí plošina by měla mít možnost nějakým způsobem zafixovat vírník ve výchozí poloze. Ať už z důvodu pojezdu auta bez předpokladu startu nebo uvedení vírníku do vodorovné (rovnoběžné s autem) polohy pro usnadnění přizpůsobení autopilota.

Toto by šlo vyřešit tím, že kardanův závěs bude umístěn pevně v jednom místě a okolní "podlaha" (podpěry vírníku) bude výškově nastavitelná. Tím zároveň může dojít k plynulému nastavování rozsahu volnosti ve všech osách.

Při rozjezdu s předpokladem startu by se nejdříve auto rozjelo na určitou rychlost a teprve poté by se podložka pomalu snížia (zvětšila by se volnost kardanova kloubu do uvedených mezí). Rychlost uvolňování by byla podle toho, jak se regulátor dokáže plynule přizpůsobovat.

kaklik, 2018-09-11:
To by ale znamenalo, že kromě ovládání elekromagnetu by se se musela ovládat ještě výška podložky.  Pokud by to skutečně bylo nutné takhle řešit, tak je asi lepší vertikálně posouvat uchycení kardanova závěsu třeba vertikálním trapézovým šroubem na krokovém motoru.

Myslel jsem, že by zafixování pro převoz bylo řešeno uchycením podvozkových ližin do tištěných U profilů našroubovaných na překližku, kde budou i kola.
Při přípravě pro start by se jenom sundaly upínací pásky a ližiny by ležely v profilech, dokud by nedošlo k nadzvednutí.

Teď mě napadlo, že to jde vylepšit tím, že by profil pro ližiny měl směrem nahoru rozšiřující se tvar, takže by s roztoucí výškou nadzvednutí stoupala i volnost do stran.

kaklik, 2018-09-11:
Tady je rychlý náčrtek toho, jak bych si to zhruba představoval.

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

Ještě to rozkreslím na dílčí komponenty.

kaklik, 2018-09-17:
Přesunutí příspěvku @roman-dvorak

Přemýšlel jsem dnska o té Markovo připomínce/otázce, proč je to tlačné a né tažné.

Je pravda, že s tažným závěsem by jsme možná získali podstatně větší stabilitu letadla na závěše, protože by to byla stabilní poloha. Takhle se to vychýlí ze středu a bude v nestabilní poloze. Dokud nebude mít vírník větší tah než rychlost auta.

Zato v případě tažného závěsu by letadlo bylo stále ve stabilním stavu a odepnulo by se v bodě, kdy tah je nulový  a letadlo by okamžitě přidalo na svém výkonu.

Samotný závěs by mohl být tažný, ale umístěný více v zadu než AZ (YAW) točna a tím by zde opadnul problém s tím, že letadlo má vystartovat dopředu. Kotva na letadle by byla umístěna v zadní části podvozku stejným způsobem. Možná by to mělo výhod, že by kontva moha být napevno přidělána a jen by se otáčel magnet na závěsu. Snad je to z následujícího schématu vidět případně překleslím.

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
(rozhodně není v měřítku)

díly nakreslené v #156

kaklik, 2018-09-17:
Tohle řešení by zřejmě bylo vhodnější. Protože nedestabilizuje celý systém. Ideální by zřejmě bylo, aby ty rotační osy procházely těžištěm UAV, pak by vliv na změnu stability byl neutrální.

Ten tenzometr bych asi z prvních pokusů vyjmul a nejdřív vyzkoušíme jak se to chová bez něj.  Myslím, že je dost možné, že k ničemu ani nebude potřeba.

kaklik, 2018-09-17:
Ještě je možná zajímavý tenhle obrázek, který ukazuje, jak se měří síly ve skutečném aerodynamickém tunelu.

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

roman-dvorak, 2018-09-17:
Myslím, že umístění rotace v ose Roll je špatně ve "třetím dílu". Protože při náklonu v Roll se vírník bude otáčet po velké kružinci okolo třetího dílu. Což mi nepřipadá dobře. Tato rotační osa by měla být taktéž co nejblíže těšišti a ose Roll na vírníku.

A zde by mohl vzniknout "čtvrtý díl", který by řešil rotaci ve dvou osách zároveň. Rotaci v ose Roll tak, že by přímo do magnetu byl M8 inbus šroub. V tom samém dílu by byla volnost v ose Pitch (Podruhé!) aby zde nedocházelo ke kroucení mezi magnetem a kotvou.

kaklik, 2018-09-17:
S tou vzdáleností od osy rotace maš úplně pravdu.  Jenom si teď nedovedu moc představit ten nový čtvrtý díl.
Dovedl by jsi ten díl nakreslit?

S tím jestli  se pod virník vejdeme bych si zatím nedělal moc starosti.  Vírník můžeme nad desku zvednout tím, že pod ližiny dáme nějaké podložky. Zkomplikuje to akorát montáž rotoru. Nemusí být navíc nutně uchycený za ližiny ale můžeme klidně použit tu vertikální trubku, pro třetí kolečko, která je teď nevyužitá.

roman-dvorak, 2018-09-17:
"čtvrtý díl" bude nějaká spojka, pomocí které se spojí 2 M8 závitové tyče. Pro vodorovnou tyč bych navrhoval ukončit uvnitř dílu. Do dílo by byla kapsa pro M8 matici a z venku by se to stáhlo proti této matici. Svislá závitová tyč by byla skrz snažená z vnější stran maticí. Toto řešení navrhuji udělat z důvodu, aby výška tohoto zařízení byla co nejmenší.

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
(Na obrázku je to nakresleno přesně obráceně)

"Pátý díl" se nasadí na M8 závitovou tyč. Uvnitř tohoto dílu bude kapsa pro matici a stáhne se to oproti druhé matici z venku. V horní části tohoto dílu bude díra pro osu ALT (pitch).

"Šestý díl" bude pomocí takově vydlice nasazen na "pátý díl". Ložiska jsou uložena z vnější strany tohoto dílu. V horní části budou z obou staran znovu vložena ložiska a pomocí šroubu M8 to bude zašroubováno přímo do těla magnetu. Na horní straně budou takové dva "výběžky", které budou nastavovat rozsah rotační osy tohoto kloubu. Skrz tyto výběžky budou zašroubovány nastavovací šrouby skrz matice zasunuté do kapes v tomto díle.

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

Mezi "Šestým dílem" a magnetem bude "Sedmý díl", který bude mít stejný průměr jako magnet a na sobě takový "trn" který toto omezí. Trn může být vystužen zašroubováním šroubu do těla trnu (ze strany od magnetu) Okolo díry pro M8 šrob by bylo vhodné udělat osazení, které by tlačilo na střední část ložiska.

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

kaklik, 2018-09-29:
Aktuální chyby v návrhu:

- Díl 888_3007 má špatnou velikost matek pro připevnění příruby EMFS-17.

kaklik, 2018-10-03:
Tak velikost děr pro matky jsem vyřešil.
A nový způsob upevnění k magnetu také.
Takže zbývá jenom nalézt metodu, jak počítat tvar závěsu pro zvětšení rozsahu úhlů. Na tom pracuje @roman-dvorak.

kaklik, 2018-10-03:
Aktuálně držák na autě vypadá takto:

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

Elizaa62, 2018-11-20:
Jak to vypadá s tímto issue?

kaklik, 2019-02-04:
Tenhle úkol se zatím stabilizoval na použití pevného sloupku s elektromegnetem.
Budoucí problém je změna konstrukčního uspořádání tak, aby držák pro start umožnil i umístění nákladu na UAV.

Closed 2019-02-04.

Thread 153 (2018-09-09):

Přípravek pro zkracování šroubů

kaklik, 2018-09-09:
Na zkrácení šroubů do kování rotorových listů by se hodil přípravek, do kterého se zašroubuje šroub (proti matici na opačné straně přípravku) a pak se pilkou na železo prořízne štěrbina v definované vzdálenosti od hlavy šroubu.
Tím by mělo být možné opakovaně řezat šrouby stejné délky.

Podobné řešení už existuje pro řezání trubek. viz https://github.com/kaklik/Components/blob/master/src/manufacturing_helpers/tube_cutter.scad

Potřebná délka uříznutého šroubu je 21,5mm.

Elizaa62, 2018-09-11:
Je uveden jako "screw_cutter".

kaklik, 2018-09-13:
Tak jsem trochu upravil rozměry a vytiskl to.
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

Myslím, že to funguje :)

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

Akorát asi bude potřeba šroub do přípravku uchytit samojistnou maticí, protože se při řezání povoluje.

Closed 2018-09-13.

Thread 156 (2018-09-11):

Díly pro uchycení elektropermanentního magnetu a UAV

kaklik, 2018-09-11:
Při uchycení podvozku vírníku na desku na střešním nosiči musí být umožněna jistá volnost pohybu minimálně ve dvou rotačních osách.  Viz #146
K tomu je potřeba užít kardanův závěs s omezeným rozsahem pohybu.  Rozsah pohybu může být omezen tvarem.
Jako čepy pro spojení jednotlivých dílů bych navrhoval použít šrouby M6  nějakých standardních délek s inbus hlavou.

Magnet, který máme  je typ EPPM-6329-24-020 s průměrem 63mm.
https://www.magnety.cz/pridrzne-elektromagnety/pridrzne-elektromagnety-s-permanentnim-magnetem/

kaklik, 2018-09-12:
Zkusil jsem udělat náčrtek, jak by konstrukce závěsu mohla vypadat.
Pro spojení předpokládám použití šroubů M6 a samojistných matic zapuštěných v kapsách. Šrouby se do matic nebudou úplně dotahovat a tím vznikne možnost protáčení v kloubových spojích.

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

roman-dvorak, 2018-09-16:
### První díl (AZ, YAW) bude řešit rotaci kolmo na střechu auta (YAW osu auta).

tento díl by se pomocí 2-4 M6 šroubů přidělal do dřevěné desky (18mm). Skrz tento díl povede licovaný šroub 8mm M6, který bude zespoud (od dřevěné desky přidělán bezpečnostní maticí). Pod maticí bude ložisko 608. Stejné ložisko bude i shora, kde z horní strany pnese druhý díl.

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

### Druhý díl (ALT)

Druhý díl bude přidělán na první díl pomocí stejného lícovaného šroubu. V této části bude hlava šroubu a povede směrem dolů. Možná by stálo za to, místo, kde bude hlava šroubu udělat širší pro možnost podložky pro roznesení síly.

Z tohoto dílu, směrem dozadu, povede "výběžek", ve kterém bude zašroubován šroub (M6?) směrem dolů. Bude vytvářet takový "trn" pro omezení volnosti rotace v AZ ose.

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

Z boků do tohoto dílu povede další lícovaný šroub, který zajistí rotaci v ose ALT.

### Třetí díl.
Tento díl bude jednoduchá kostka, kterou skrz na skrz povede lícovaný šroub z druhého dílu. Ve spodní části ním bude prostrčena M8 závitová tyč. Tato tyč bude uložena rotačně pomocí radiálních ložísek 608 z boku dílu. Ložiska budou z každé strany stažěna maticí M8.

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

Na konci závitové tyče bude umístěn tenzometr a magnet. Je vybrána závitová tyč M8, která už je dostatečně pevná a navíc v magnetu je M8 závit. Na druhé straně musí být závaží, které bude vyrovnávan nevyváženost soustavy.

### Celek...
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

kaklik, 2018-09-17:
Souhlasím, jenom bych kvůli konstrukčnímu zjednodušení navrhoval díl První díl (AZ, YAW) tvarově upravit tak, aby vycházel z kuželu.

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

Zapsáno jako

    cylinder(h=50, r1=50, r2=30, center=false);

Odpadne tím požadavek na ta žebra a celkově se to myslím zjednoduší i pro tisk.

Ostatně u druhého dílu (ALT) by to mohlo být podobné.

[Rozměry ložiska 608](https://www.arkov.cz/p/608-2zr-lozisko-kulickove-jednorade-oboustranne-kryte-plechem-zkl-13967)

kaklik, 2018-09-17:
Tohle jsou lícované šrouby průměru 8mm/M6, které máme  k dispozici
Délky jsou 70 a 30mm.  Pro ukázku je na fotce ještě ložisko 608 a čep 8mm / 40mm, který ale do ložiska nejde prostrčit.

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

kaklik, 2018-09-18:
"čtvrtý díl" bude nějaká spojka, pomocí které se spojí 2 M8 závitové tyče. Pro vodorovnou tyč bych navrhoval ukončit uvnitř dílu. Do dílo by byla kapsa pro M8 matici a z venku by se to stáhlo proti této matici. Svislá závitová tyč by byla skrz snažená z vnější stran maticí. Toto řešení navrhuji udělat z důvodu, aby výška tohoto zařízení byla co nejmenší.

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
(Na obrázku je to nakresleno přesně obráceně)

"Pátý díl" se nasadí na M8 závitovou tyč. Uvnitř tohoto dílu bude kapsa pro matici a stáhne se to oproti druhé matici z venku. V horní části tohoto dílu bude díra pro osu ALT (pitch).

"Šestý díl" bude pomocí takově vydlice nasazen na "pátý díl". Ložiska jsou uložena z vnější strany tohoto dílu. V horní části budou z obou staran znovu vložena ložiska a pomocí šroubu M8 to bude zašroubováno přímo do těla magnetu. Na horní straně budou takové dva "výběžky", které budou nastavovat rozsah rotační osy tohoto kloubu. Skrz tyto výběžky budou zašroubovány nastavovací šrouby skrz matice zasunuté do kapes v tomto díle.

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

Mezi "Šestým dílem" a magnetem bude "Sedmý díl", který bude mít stejný průměr jako magnet a na sobě takový "trn" který toto omezí. Trn může být vystužen zašroubováním šroubu do těla trnu (ze strany od magnetu) Okolo díry pro M8 šrob by bylo vhodné udělat osazení, které by tlačilo na střední část ložiska.

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

kaklik, 2018-09-18:
@Elizaa62  Správně jsou ty nákresy od @roman-dvorak

Elizaa62, 2018-09-18:
Díl první jako díl 888_3000.
Díl druhý jako díl 888_3001.

roman-dvorak, 2018-09-18:
Na díl 888_3000 je potřeba přidělat časti pro omezení rotace v YAW ose.

@Elizaa62 Po domluvě s @kaklik by to chtělo na díl 888_3000 přidělat takové "sloupky", vyšší než je současná výška dílu. Na mém nákresu výše je to trochu vidět. Skrze tento díl umístit sroub, kterým by se nastavoval rozsah volnosti osy a tento šroub by narážel do výběžku z dílu 888_3001. Matice by byla umístěná v kapse přímo v tom sloupku.

Z výběžku na dílu 888_3001 by se mohla odstranit díra, která byla původně myšlená na trn směrem dolú, který by měl stejný účel.

roman-dvorak, 2018-09-19:
@Elizaa62 "Čtvrtý díl" a "pátý díl" by bylo možné spojit v jeden. Viz. následující nákres
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

Udělal bych to spíše tak, že "díl 4+5" by byl jako vidlice a "šestý díl" by se vkládal dovnitř. Ostatní díly by měly zůstat stejné.

Elizaa62, 2018-09-19:
Doplněny sloupky k dílu 888_3000 i s otvorem pro šroub a kapsou pro matku. Akorát si nejsem jistá, zda správně.

Zvětšeny rozměry dílu 888_3001 a odstraněn otvor pro šroub ve výstupku.

Nový díl 888_3002 -  třetí díl z tohoto issue.

Nový díl 888_3003 - sestava předchozích třech dílů.

roman-dvorak, 2018-09-19:
@Elizaa62 úplně správně ne :)

Má to být tak, že díl 888_3001 se má na dílu 888_3000 otáčet v omezeném rozsahu (cca 10deg) A šrouby vložené do těch výstupků z dílu 888_3000 mají nastavovat rozsah, jak moc se může otáčet.

Takže je potřeba přidělat kapsu i do druhého sloupku.
Výstupek z dílu 888_3001 bych udělal trochu uzší a odstranit díru skrz.
Sloupky z dílu 888_3000 udělat dál od sebe a udělat větší mezeru mezi sloupkem z dílu 888_3000 a válcovou základnou dílu 888_3001

Nápad od @kaklik, že by to bylo bez žeber a byl by to kužel není špatný, protože by se tím velmi zvýšila pevnost těchto výstupků.

kaklik, 2018-09-19:
Nezavedeme si nějakou konvenci v těch názvech?  vytvořit sestavu z dílů je dobrý nápad, ale chtělo by to pojmenovat nějak aby bylo jasné, že to sestava té skupiny.

Zatím  to máme odlišené jako

- 666_ výkresy od pana Dobiáše.
- 888_ naše nové výkresy

A pak je zevedeno číslování skupiny jako třeba  888_3XXX jsou díly závěsu.  Tohle mi připadá dobré.
Akorát bych to ještě rozšířil o sestavy a zavedl třeba 888_31XX konkrétně třeba 888_3101. Za předpokladu, že skupina dílů nebude mít víc jak 100 komponent. Pak by to asi přestalo fungovat.

Jde mi o to, že když se sestavy budou číslovat stejně jako díly, tak bude existovat sestava 888_3003 a další díl skupiny bude 888_3004. Což mi přijde dost nepřehledné.

Elizaa62, 2018-09-20:
Sestava přejmenována na 888_3101.scad

888_3003 - čtvrtý a pátý díl
888_3004 - šestý díl
888_3005 - sedmý díl

roman-dvorak, 2018-09-20:
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

Díl 3004 by měl být dole půlkruhový, aby se mohl v dílu 3003 otáčet. To že nepůjde naklonit dopředu dolů nevadí. Musí jít naklánět "dozadu".

Díl 3004 musí být širší a zarážky pro omezení roll rotace dále od sebe. Aby se díl 3005 mohl otáčet alespoň o 10deg na každou stranu. Ze stejného důvodu musí být díl 3004 nižší.

roman-dvorak, 2018-09-20:
@Elizaa62 Když si prohlížím takhle ten složený díl, tak vzhledem k rozměrům a potřebné volnosti roll osy (minulý komentář) by možná bylo lepší vidlici udělat na díl 3004 a díl 3005 do toho vkládat. Omlouvám, se že jsem to navrhoval původně obráceně. Nedokázal jsem si dobře představit rozměry.

To zapuštění ložiska do vnitřní strany vidlice je fajn nápad. Ale blbé je, že když se šroub stáhne ze stran maticí, tak se nebude otáčet a nemá tam to ložisko moc smysl. Proto by bylo dobré to udělat podobně jako je to na mé modifikací dílu 3002. A vlastně ten díl 3003 lze vytvořit modifikací dílu 3002 tak, že se přidá uložení pro ložisko i do druhé díry a trochu se protáhne.

Elizaa62, 2018-09-20:
Pokusila jsem se to opravit.

kaklik, 2018-09-21:
Díly 3003 a 3004 do sebe pasují velmi na těsno. není tam žádná vůle pro separační podložky u ložisek.

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

Tohle se netiskne moc dobře.
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

Ve spodním dílu není žádná rezerva na délce šroubu a šroub sotva dosahuje do spodního ložiska
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

kaklik, 2018-09-22:
Díry pro hlavy šroubů M6 v základně by měly být spíše šestihranné,  protože takto jdou použít pouze šrouby se šestihrannou hlavou.

kaklik, 2018-09-29:
V dílu 888_2006 chybí kapsy na zapuštění matic šrobů M2.5 od serva.

kaklik, 2019-02-04:
Pro současnou aplikaci řešení vyhovuje.

Closed 2019-02-04.

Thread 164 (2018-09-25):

Tisknutelný díl pro montáž rotorové hlavy na pilon

kaklik, 2018-09-25:
Plechové díly 666 1021 a 666 1022 mají být nahrazené jedním tisknutlým dílem s kloubovým ložiskem [EFSM-12 ](https://www.igus.cz/product/382).

roman-dvorak, 2018-09-25:
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

kaklik, 2018-09-26:
Prohlédl jsem si to a myslím že ten díl je už z velké části hotový. Našel jsem zatím jenom tyhle nedostatky

- chybí díry na šrouby od serva,
- drážka na kolík z desky hlavy je otočená o 90 stupňů
- prostřední díra pro kulové ložisko je malá. Měla by mít průměr 25mm.
- servo by mělo být blíže k pravému okraji dílu vychází mi to podle výkresu asi na 4mm od hrany plechu.
- stěna pod ložiskem by myslím měla být tlustší, bude se přes ní přenášet celá hmotnost.

kaklik, 2018-09-26:
Ještě jsem si všiml, že ty rozměry, které tam jsou zřejmě nejsou pro přírubu EFSM-12 ale pro menší EFSM-04. Na tom odkazu je totiž potřeba si překliknout na správný typ. Potom jsou rozměry následující:

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

Parameter | Value
-- | --
Ø d1 | 12,00 mm
Ø dB | 25,0 mm
h | 40,0 mm
m | 28,0 mm
A1 | 7,0 mm
Ag | 13,0 mm
N | 5,3 mm

kaklik, 2018-09-27:
Tak díl jsem vytiskl.  Pozitivní je, že do něj pasuje příruba s kulovým kloubem. :)
Jsou tam ale i nedokonalosti.

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

Například tyto:
- Nejde prostrčit servo do otvoru, protože tomu brání jeho kabel. Řešením je zvětšit otvor na kabely ve směru osy Y.
- Ovory pro upevnění serv mají špatnou rozteč ve směru osy Y.

kaklik, 2018-10-03:
Dobře, po téhle úpravě by to pak mělo být stejně široké, jako původní díl. To by mělo být správně. :)

U toho čepu jde o to, že při pohybu ve směru osy X naráží do okrajů toho otvoru. Nevím o kolik to je, ale zřejmě je potřeba jednak zvětšit ten otvor, a potom i zvětšit poloměr podstavy toho kuželu, kterým je otvor vytvořen.  To by mělo zajistit, aby se čep mohl pohybovat ve větším rozsahu úhlů a po větší vzdálenosti.
Rozsah úhlů ve kterých se čep může pohybovat je asi +/- 20 stupňů.

kaklik, 2018-10-19:
Zjistil jsem, že by bylo zřejmě lepší tenhle díl upravit tak, aby se na trubku šrouboval fixní délkou šroubů.  S tím že hlavička a matka šroubu bude v dílu trochu zapuštěná. Vhodný šroub je například M4x50, neboť je potíž sehnat delší šrouby.

Closed 2018-12-29.

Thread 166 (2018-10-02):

Aktualizace sestavy podle současného stavu

kaklik, 2018-10-02:
Soubory ve složce https://github.com/Elizaa62/Components/tree/master/src/drawings

Už neobsahují přiliš aktuální stav celkové sestavy.  Bylo by proto zřejmě vhodné sestavu aktualizovat.

Elizaa62, 2018-12-29:
Sestava je aktualizovaná pod názvem 666_2000.  Sestavu pod názvem 888_1005 jsem smazala, aby nedošlo k záměnám.

Elizaa62, 2018-12-29:
> Sestava je aktualizovaná pod názvem 666_2000. Sestavu pod názvem 888_1005 jsem smazala, aby nedošlo k záměnám.

kaklik, 2019-02-04:
Rozměry trubek jsem přidal přímo jako fotografie do úlohy řešení ohýbacího přípravku #119

kaklik, 2019-05-31:
- V modelu chybí pohyblivé části směrovky
- Některé díly třeba kryt rotorové hlavy není upraven, aby pasoval k současnému stavu modelu

Elizaa62, 2019-06-10:
Koukala jsem, že díl A spodního krytu je opravená. Opravila jsem podle rozměrů podvozkové trubky.

Mohl bys mi prosím napsat seznam dílů, které se měnily a tudíž nepasují do sestavy?

Kryt rotorové hlavy je který díl?

kaklik, 2019-06-10:
Dílů, které do sestavy nepasují díky tomu, že se měnily je minimum.
Je to v podstatě akorát:
-  [Kryt vertikální trubky](https://github.com/ThunderFly-aerospace/TF-G1/blob/master/STL/666_1032.stl)
-  Navázání držáku motoru k hornímu krytu

Horší je to ale s díly které v sestavě chybí úplně.  Ideálně by sestava totiž měla obsahovat všechny tyto komponenty:

- vrtule
- rotor
- sestava rotorové hlavy
- okrytování těla vírníku (možná s krytem motoru)
- ocas včetně pohyblivých částí
- podvozek přední
- podvozek zadní
- kolečka včetně středu

rotorové listy, závaží a kování máme namodelované jako jednotlivé komponenty, je z toho však potřeba vytvořit podsestavu.

Elizaa62, 2019-06-10:
A k těm chybějícím dílům máš když tak jejich čísla? Abych to nemusela hledat a zkoumat.

kaklik, 2019-06-10:
Aktualizoval jsem ten můj předchozí komentář o odkazy na díly, které teď aktuálně máme.
Ještě mě napadlo, že by ti možná ušetřilo práci a čas, kdyby jsi tyto díly do té sestavy[ importovala jako už vyrenderované STL soubory](https://en.wikibooks.org/wiki/OpenSCAD_User_Manual/STL_Import_and_Export#import). Pak bys nemusela čekat, až se vyrenderuje celá sestava.

Tento proces bude minimálně nutný v případě rotorového domku, protože ten nemáme jako openscad soubor, ale pouze jako STEP model, který ti překonvertuju na STL přidám mezi komponenty.

Elizaa62, 2019-06-12:
Vytvořila jsem sestavu rotorových listů s podložkami a kováním, ale bez závěsu. Nejsem si jistá, jak to tam vše patří.

kaklik, 2019-06-12:
Ta hláška je způsobená tím, že někdo udělal změny v repozitáři mezitím, co jsi něco upravovala. Nemělo by to být nic hrozného a  mělo by stačit spustit git pull.

Teď se mi taky podařilo exportovat [díl rotorového domku](https://github.com/ThunderFly-aerospace/TF-G1/blob/master/STL/666_1207.stl).

kaklik, 2019-06-13:
Vytvořil jsem ti [příklad](https://github.com/ThunderFly-aerospace/TF-G1/blob/master/src/666_1207.scad) jak importovat už hotové díly do sestavy.

Tenhle nový způsob považuji za důležitý kvůli tomu, že to je megarychlá metoda, jak skládat sestavy z vyrenderovaných dílů. Kde nemusíš čekat, až se ti překreslí sestava.

kaklik, 2019-06-17:
Ta vrtule v té sestavě je, akorát má špatnou velikost a je na nečekaném místě.

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

kaklik, 2019-06-17:
Tak problém s vrtulí jsem částečně vyřešil tak, že jsem model vrtule v meshlabu přeškáloval na reálnou velikost v milimetrech.

roman-dvorak, 2019-06-18:
dílčí sestavy byly složeny v blenderu. Výsledek je takový:

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

rotorové listy byly do modelu vloženy ručně, protože je nebylo možné vyrenderovat v sestavě.
Místo prerotátoru byl přidán válec.

kaklik, 2019-06-18:
@Elizaa62  Aby se tohle issue mohlo uzavřít a příště nebylo potřeba tu sestavu skládat v blenderu, tak je potřeba vyřešit ty nezaškrtnuté body výše.

Měly by ti k tomu chybět akorát rozměry válce jako hlavního motoru, které jsou průměr 49.5 mm a výška 49 mm .

kaklik, 2019-08-07:
Myslím, že tohle je pro aktuální stav vírníku vyřešeno.

Closed 2019-08-07.

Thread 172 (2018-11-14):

Úprava držáku motoru 666_1026

kaklik, 2018-11-14:
Protože tisknutý díl 888_1015 už úplně nahradil spojku 666_1026 na rotorové hlavě, tak už není potřeba aby spojka 666_1026 zachovávala svůj tvar společný pro obě umístění.  Je tak možné zjednodušit uchycení motoru.  Tím že se ze spojky vytvaruje díl specifický pro motor.

Původní idea uchycení motoru plechem byla takováto:

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

Nejproblematičtější částí jsou ohyby plechu, které je těžké vyrobit přesně.

Do zakótovaných otvorů měly patřit šrouby dílu 666_1026. Nyní by ale díl 666_1026 bylo možné tvarově upravit tak, aby plech pro uchycení motoru nebyl potřeba.  Zároveň není nutné mít nastavitelný náklon seřízení motoru protaženým otvorem pro šroub. Neboť úhel může být nastaven přímo parametrem vytištěného dílu.

Potenciální komplikace úpravy je  snížení  možnosti chlazení motoru odvodem tepla do plechového dílu. To ale lze vyřešit zachováním plochého plechu pouze v přední části bez ohybů.  Následující úkoly proto jsou:

- [x] Upravit tvar dílu  888_1026, tak aby obsahoval i boční stěny v původním návrhu tvořené plechem. V těchto bočních stěnách bude zapuštění pro matky.
- [ ] Vytvořit nákres předního plechu tak, aby plech bylo možné přišroubovat z přední strany k dílu 888_1026, za kapsy pro matky umístěné v bočních stěnách dílu 888_1026

roman-dvorak, 2019-10-06:
Motorový díl pro nový vírník může být o něco nižžší a zároveň může mít menší sklon osy motoru.

kaklik, 2019-10-07:
Tohle issue je k dílu, který už neexistuje. Vytvořil jsem pro to nové issue #252.

Closed 2019-10-07.

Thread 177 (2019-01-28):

Držák na střechu auta pro transport  a omezení na jednu osou volnosti

roman-dvorak, 2019-01-28:
Pro potřeby vývoje SW a nastavování regulátoru by bylo potřeba vyrobit držák, který bude umožňovat pohyb pouze v ose [Roll](https://simple.wikipedia.org/wiki/Pitch,_yaw,_and_roll). Osy Pitch a Yaw by měly být pevně zafixovány. Držák by měl vírník podpírat pod ocasní částí pomocí "dvojnožky". Držák by měl jít snadno demontovat nebo nějak sklopit.

Tento držák je rozšíření issue #146

Na následujících obrázcích je můj návrh tohoto držáku.
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

Spodní díly 1-1 a 1-2: Spodní díl bude přišroubován jedním šroubem (rozdíl oproti obrázku) do nosné desky na střeše auta. K dílu 1-1 bude pomocí šroubu přidělán díl 1-2. Spolu budou tvořit kloub, který celý držák umožní sklopit dozadu. Díl proto musí mít na rozdíl od obrázku zaoblené rohy na otočné části, aby nepřekážely při otáčení.
Do dílu 1-2 budou nastrčeny AL trubky a sešroubovány pomocí šroubu skrz.
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

Díl 2-1 a 2-2 Pevně spojí trubky od patek. Trubky zde budou znovu prošroubované.
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

Vrchní díl umožňí připevnit horizontální trubku vírníku. Je potřeba mít možnost naklonit tento díl podle sklonu vírníku.
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

roman-dvorak, 2019-01-29:
Výška středu horizontální trubky vírníku nad základní deskou je 28 cm. V první řadě je potřeba vytvořit držák, který bude v roll ose volný. Tzn. ocasní trubka se v držáku musí volně protáčet.

kaklik, 2019-01-30:
Nějakým speciálním protáčením bych to teď nekomplikoval. Myslím že stačí když se na tom dílu, co stahuje trubku úplně nedotáhnou šrouby.

Elizaa62, 2019-02-02:
V tomto issue jsem vytvořila díl 1.1 a 1.2 jako díl 888_3011.scad. Bylo by možné vytvořit pull_request, abych si mohla stáhnout i další vytvořené díly?

kaklik, 2019-02-02:
pull-request obsahující nový držák jsem vytvořil.

kaklik, 2019-02-04:
Tak se po posledním testu ukázalo, že držák je potřeba mírně snížit.  Ovšem do desky na střeše TF-R1 jsme navrtali díry pro současnou rozteč patek držáku.

Rozteč by měla být patrná z následujících fotografií a je to potřeba přepočítat na rozteč děr v patkách.

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

Aby nebylo potřeba vrtat nové díry, tak je nutné tuto současnou vyvrtanou rozteč děr zachovat.
Držák pak lze snížit buď

- snížením výšky patek, což jde, neboť teď je zapuštění pro šrouby k desce zbytečně vysoké a stačila by výška pouze na matku M6.
- Změnou délky trubek, což ale přináší i nutnost zmenit úhel trubek v držáku. Trubky jsou teď dlouhé 199mm.

Elizaa62, 2019-02-07:
díl 888_3015.scad

Elizaa62, 2019-02-08:
Patky opraveny.

kaklik, 2019-02-11:
Držák funguje.

Closed 2019-02-11.

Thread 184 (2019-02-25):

Nový testovací přípravek na měření charakteristik rotoru

kaklik, 2019-02-25:
Pro měření rotoru by bylo potřeba vytvořit nové díly vycházející ze současné konstrukce rotorové hlavy.
Tak aby bylo umožněno rotor naklonit pod definovaným úhlem dozadu a měřit jeho vztlak a odpor. Náklon rotoru do stran není třeba uvažovat.
Důležitá je fixace náklonu v nastavitelném úhlu v rozsahu 0° (vodorovně) až -30° (sklon dozadu).

Elizaa62, 2019-05-05:
Víš trochu přesněji, jak si toto představuješ?

kaklik, 2019-05-05:
Bylo několik variant na kterých jsem se chtěl domluvit.
Nyní to vypadá, že konstrukční řešení se už ustálilo na nějakém [takovémto provedení](https://github.com/ThunderFly-aerospace/Auto-G2/issues/10).

Což znamená, že díl který bys měla nakreslit bude vypadat přibližně nějak takto:

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

Jeho smyslem je, že bude držet rotor a snímač otáček. Celý se přišroubuje čtyřmi šrouby M4 k horní části [tohoto dílu](https://github.com/ThunderFly-aerospace/TF-R1/blob/master/CAD/STL/888_5008.stl). (Z důvodu tisku je díl otočený vzhůru nohama, takže montážní otvory jsou dole).
@cesilko1  pro montážní díl rotoru připravil [knihovní prvek](https://github.com/ThunderFly-aerospace/TF-R1/blob/master/CAD/src/lib/rotor_joint.scad), který  by mohl konstrukci dílu usnadnit.

Somotný nový díl může vycházet z [existujícího dílu rotorové hlavy](https://github.com/ThunderFly-aerospace/TF-G1/blob/master/STL/888_1020.stl). Ze kterého je potřeba odebrat části, které nejsou potřeba. (Zapuštění pro kulové ložisko a výstupy pro páky serv)
Naopak je potřeba na díl přidat z knihovny otvory pro montážní šrouby k [naklápěcímu dílu](https://github.com/ThunderFly-aerospace/TF-R1/blob/master/CAD/STL/888_5008.stl) měřícího přípravku.
Taktéž je potřeba ze spodní strany připravit otvor pro šestihrannou matici M6 hlavního šroubu rotoru, který přitahuje ložiska, jak je nakresleno v náčrtku výše.

kaklik, 2019-08-06:
Tohle je vyřešeno [tímto dílem](https://github.com/ThunderFly-aerospace/force_balance/blob/master/cad/STL/888_5012.stl)

Closed 2019-08-06.

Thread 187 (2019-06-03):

Vypouštěcí zařízení pro start z lana

roman-dvorak, 2019-06-03:
Do dílu 888_1026 (Držák tažného motoru) je potřeba integrovat vypouštěcí zařízení, které umožní odpojit tažné lano pomocí dálkového ovladače a serva na vírníku.

Princip zařízení je vidět na tomto orázku:
http://www.gliders.uk.com/images/0723470.jpg

V dílu 888_1026 bude podélná štěrbina. U vstupu bude vysoká, aby umožňovala velký úhel tažného lana, a její výška se bude postupně snižovat. Příčně, přes tuto díru, bude osa - dlouhý M3-A2 šroub. Tento šroub je potřeba orientovat tak, aby nedocházelo k jeho povolení tím, že se o něj bude lano smýkat.. O tuto osu se z horní strany bude opírat ocelový drát veducí až k servu, které bude za drát tahat. Po vytažení ocelového drátu servem dojde k uvolnění lana.
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

Navrhovaná realizace je na následujících náčrtcích:

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

Předpokládané umístění serva je takto:
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
Servo je potřeba, vzhledem ke směru tisku, orientovat tímto směrem.

Je potřeba brát v ohled, že se skrze tento díl se přenáší veškerý tah motoru a je tedy potřeba co nejvíce zachovat jeho pevnosti.

kaklik, 2019-06-28:
Nepodařilo se mi přijít na to jak je ta konstrukce vymyšlená.  Jedinné umístění serva ve kterém tam pasuje je toto:

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

Tohle řešení ale má několik problémů.

1. Páka serva nevychází naproti drážce pro páku a táhlo.
2. Servo drží pouze na jednom šroubu
3. Přesahuje mimo model do zadní části

Při konstrukci dílu je třeba také myslet na to, že na díl má pak nějak navazovat [horní kryt](https://github.com/ThunderFly-aerospace/TF-G1/blob/master/STL/666_1025.stl).

roman-dvorak, 2019-07-07:
@cesilko1 Myslíš, že takto je to hotové? Mě přijde ta drážka pro příchytku serva dost úzká. Jak je v modelu široká? Jsou tam započitané dostatečné tolerance?

cesilko1, 2019-07-07:
@roman-dvorak jestli jsem správně pochopil tohle http://file.yizimg.com/357982/201719-11844730.pdf tak je ta drážka o 0.5mm větší

kaklik, 2019-07-09:
Mě přijde že tam je hrozně málo místa pro páku serva a taky na úchyt táhla na páku serva.

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

roman-dvorak, 2019-07-11:
Vidím další změny..
https://github.com/ThunderFly-aerospace/TF-G1/blob/master/STL/888_1026.stl

Takhle se mi to už líbí podstatně více. @kaklik co si o tom myslíš teď?

kaklik, 2019-07-17:
Ten model je původně plánovaný pro tisk v [této pozici](https://github.com/ThunderFly-aerospace/TF-G1/blob/master/STL/print_plate_1026_engine.stl).

Nevím jak se vytiskne ten převislý držák serva. Nechal jsem to tisknout s podporami a uvidíme, jaký bude výsledek.

roman-dvorak, 2019-07-20:
Pro tisk bez podpor je potřeba do dílu namodelovat podpory ručně v místě serva a vytvořit drážku pro vyvedení kabelu serva.

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

kaklik, 2019-07-22:
Takhle konstruovaná podpora integrovaná do modelu nebude dobře fungovat.

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

Je potřeba aby byla co nejtenčí. Ideálně jen velmi málo nad 0.61mm. Zároveň je také potřeba aby podpírala převis v celém profilu a nebo, aby umožnila jednoznačným způsobem tisknout most.  Vzhledem k tomu, že je převis ukosený, tak to v tomhle případě jednoznačné není. Podpora by tak ukosená musela být taky.

cesilko1, 2019-07-23:
tak jsem upravil supporty, tloušťka se dá nastavit proměnnou `supports_thickness` na řádku 33

kaklik, 2019-07-30:
Rozteč šroubů pro uchycení serva je příliš velká.
V modelu jsou zřejmě použity šroby M2,5 ale reálně servo má být přichyceno šrouby M2.

Closed 2019-07-30.

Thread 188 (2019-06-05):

Návrh zadního podvozku vírníku s odpružením a tlumením.

kaklik, 2019-06-05:
Zadní kola jsou nyní odpružena deformací AL trubky, řešení funguje dobře, ale má tyto nedokonalosti.

- Deformace trubky není definovaná a může snadno dojít k nevratné deformaci, která je těžko rozpoznatelná.
- Konstrukce se špatně vyrábí, neboť je těžké správně navrtat všechny díry v trubkách

Řešením těchto problémů by mohlo být vytvoření tisknutelné vložky, která deformaci normalizuje na provedení torzní tyče tlumené třením o plastové pouzdro.

Konstrukčně to lze realizovat 3D tisknutelnou vložkou v trubce. Vložka může vypadat například takto:

(pohled v řezu tlustou podvozkovou trubkou)
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

(Pohled z boku)

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

Principem nového konstrukčního řešení je, že tenčí podvozková trubka, ke které je uchyceno kolečko je šroubem skrz díru přichycena na konci dlouhého plastového pouzdra. Celé pouzdro je pak vloženo do větší trubky.  Pozice pouzdra je pak zafixována šrouby stahovatelným límcem, který zafixuje jak natočení tak i nasunutí pouzdra na větší trubce.

Při funkci se pak deformuje krutem trobka o menším průměru uvnitř pouzdra.  Plastové pouzdro zároveň třením tlumí případné kmitání podvozku.

Nový díl by měl vzniknout úpravou již [existujícího dílu](https://github.com/ThunderFly-aerospace/TF-G1/blob/master/STL/666_1006.stl).

RomanDCZ, 2019-06-06:
Podle mého názoru je nezávislé odpružení zadních kol jednou z příčin nestabilní jízdy. Myslím, že náprava by měla být tuhá, odpružená společně. Nezávislé odpružení kol mění geometrii podvozku. Změna geometrie způsobuje změnu směru jízdy.
Ideový návrh je v příloze. Spojovací tyč musí být tuhá, odpružení může být provedeno pomocí pružných elementů v uložení spojovací tyče nebo pomocí pružin. Tlumení klidně pomocí třecího pouzdra. Z hlediska stability by měla kola mít co největší průměr ( moment setrvačnosti) a podvozek co největší rozvor a rozchod.
Těžiště letounu by mělo v půdorysu být nad těžištěm trojúhelníku tvořeného koly.
Přední kolo může opatřeno natáčením.

[podvozek_navrh.pdf](https://github.com/ThunderFly-aerospace/TF-G1/files/3263361/podvozek_navrh.pdf)

kaklik, 2019-06-06:
Tento návrh jsem nyní konzultoval s kamarádem a nejsem si jistý správností této úvahy.  Neboť za normálních okolností je nezávislost odpružení jednotlivých kol žádoucí, kvůli tomu že není chtěný stav, aby jeden hrbol vytvořil nežádoucí impulz v celé nápravě.

Při pružení nápravy skutečně dojde ke změně geometrie, ale tato změna je spíše ovlivněna konstrukcí nápravy, než nezávislostí odpružení.
Ohledne reakce na jizdní stavy by byla lepsi šikmá osu kyvu, aby kola šla do priklonu a použít nějakou sbihavost, ta stabilizuje.

Pokud ve staticke poloze jsou kola priklonena k sobe se šikmou osou kyvani, tak pri propružení jde naprava proti nezadoucimu odkloneni kola ven a stabilita je jina.

Rozdíl konstrukčního řešení je zobrazen na následujícím obrázku (vrchní obrázek je momentálně implementován).

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

S úvahou ohledně těžiště ale úplně souhlasím.

kaklik, 2019-06-18:
Z hlediska přistání je zřejmě lepší, aby podvozek byl přetlumený a absorboval energii na dlouhé dráze.
Příkladem takového podvozku může být [G-Force Landing Gear](https://www.youtube.com/watch?v=ajM3yOojPbg)
Tato konstrukce zřejmě ale nebude naopak vhodná pro start.

roman-dvorak, 2019-07-01:
Nový návrh podvozku by měl mít každou polovinu samostatně uchycenou za kostru vírníku a nezávisle a tlumenou. Tento návrh podvozku by měl zamezit, aby se kolečko nemohlo ohnout dozadu a tlumící pohyb byl prováděn pouze nahoru a dolu s tím, že při větším stlačení se kolečko bude naklánět okolo  roll (podélné) osy vírníku.

V tomto issue je celkový nákres podvozku. Jednotlivé díly budou řešeny v samostatných issues, aby bylo možné řešit jejich detaily samostatně a aby na tom mohlo snáze pracovat více lidí.

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

Podvozek se bude skládat ze dvou tyčí, které budou pevně připevněné k vidlici kolečka. Směrem k tělu vírníku se budou rozcházet. Tam budou zavěšeny za ložisko, které se bude otáčet v podélné ose vírníku. V této implementaci bychom použili Igus ložiska [Igubal stojaté ložisko KSTM](https://www.igus.cz/info/spherical-bearings-pillow-block-kst).

Mezi těmito tyčemi bude umístěn píst, který se bude stlačovat oproti existující podvozkové příčné tyči. Tlumič bude muset být připevněn na obou stranách pomocí kulových ložisek. Buď znovu  pomocí [KSTM](https://www.igus.cz/info/spherical-bearings-pillow-block-kst) nebo pomocí jiného Igubal ložiska. Např. [EFOM](https://www.igus.cz/info/spherical-bearings-flange-bearings-overview). Výběr ložiska bude záležet na konkrétním dílu. Tak, aby tam bylo co nejméně zbytečného materiálu.

K podvozku bude muset být definováno několik základních parametrů, podle kterých se budou počítat požadované úhly a podobné další rozměry.

- Výška podvozku - průnět vzdálenosti podélné tyče vírníku a osa koleček do osy Z
- Rozchod podvozku - vzdálenost koleček
- Vzdálenost připevňovacích míst k podélné trubce vírníku
- Vzdálenost připevnění pístů k příčné trubce

roman-dvorak, 2019-07-01:
Zadním podvozkem by mělo být možné zatáčet. Zatáčení bude řešené tak, že ke každému měchovému kolu #191 bude přes třecí převod připevňen motor s rotačním pláštěm. Tento motor bude sloužit jako brzda. Autopilot bude vždy jedno kolečko přibržďovat a tím bude celý vírník zatáčet. Toto řešení má několik výhod. Například to, že při startu i při přistání jsou zadní kolečka nejdéle v kontaktu se zemí.

K brždění by mělo být možné použít VESC regulátor.

RomanDCZ, 2019-07-02:
Při propružení dojde ke změně geometrie, letoun zatočí. To by musela být
doplněna ještě horní ramena.
Pak nevím, proč u pružiny musí být kulové ložiska. Tam bude stačit obyčejný
čep na každé straně.
Největším problémem bude naladění tuhosti pružiny a tlumiče.

Dne po 1. 7. 2019 18:21 uživatel Roman Dvořák <notifications@github.com>
napsal:

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

roman-dvorak, 2019-07-02:
Ano, všude by stačilo použít klasická radiální kuličková ložiska. Například ložiska z řady 608.

Ale chceme použít plastová kulová ložiska Igubal, které vydrží opravdu hodně a nevadí jim nárazy. To by mohl být v případě kuličkových ložisek problém.

Navíc tato ložiska už mají docela šikovnou přírubu, kterou lze jen přišroubovat k tištěným dílům. Tím se ušetří obrovské množství materiálu. Tím je celá konstrukce i lehčí.

Tato ložiska budou použita i u zavěšení ramen podvozku, budou se otáčet kolem jedné (společné) osy.

V obrázku je schématicky nakreslena pružina. Na vírníku to bude pneumatický tlumič, který bude mít propojené obě části přes jednostranný ventil.

kaklik, 2019-07-02:
Nerozumím úplně tomu, proč by změna geometrie vedla při této konstrukci k zatočení.   Při propružení dojde na A-ramenu k příklonu kola, což působí naopak [stabilizujícím](https://en.wikipedia.org/wiki/Camber_angle) účinkem a zvyšuje sílu potřebnou k zatočení.

kaklik, 2019-08-11:
Myslím, že konstrukční řešení zadního podvozku je již zvoleno. Nyní je potřeba dořešit realizační detaily.

Closed 2019-08-11.

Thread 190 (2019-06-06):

Nový způsob připevnění předního kola ve vlečném uspořádání

roman-dvorak, 2019-06-06:
Toto issue nezahrnuje odpružení předního kola z #189. Je to pouze alternativa k tyči, která se rozbila při pokusu o přistání. Mělo by to být bytelnější a nemít chyby z predchozí konstrukce. Navíc by to mělo být ve vlečném uspořádání (kolečko směrem dozadu - ne dopředu) To nám umožňuje použít menší servo.

Připevnění předního kola bude místo podložky pro přimagnetování na platformu v dílu #172. V dílu držáku motoru jsou dvě díry M4, do kterých se strčí dva šrouby. Ve sloupku budou teda díry na šrouby a kapsy na matky. Sloupek bude kónický.  Celý sloupek bude rozdělen na dva díly kvůli tisku. Tyto dva díly budou také sešroubovány - budou stačit pouze M3 šrouby, protože budou jen tyto dva díly držet pohromadě. Celé to bude stažené pomocí lícovaného šroubu v ose dílu. Matka M5 bude v kapse.

Spodní část bude navazovat kónicky na první (horní) polovinu. Na horní části spodní poloviny bude taková "destička" ve které bude přidělané servo pomocí dvojice šroubků.. Lépe to bude vidět na obrázku :)

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

 Je potřeba zajistit, aby táhlo od serva vycházelo kolmo na páku spodní vidlice a aby odpovídala výška páky serva a páky vydlice - je vhodné si následně udělat sestavu, ve které je toto dobře vidět.

Ještě bude potřeba změřit nějaké další rozměry toho serva. V dílu pro malý vírník nejsou dostatečné parametry - pouze šířka a hloubka.

kaklik, 2019-08-11:
Je toto ještě relevantní?

Řekl bych, že toto je již zastaralé issue, neboť v této chvíli to už musíme vyřešit lépe. Navíc neplánuji přední kolečko mít řízené.

Closed 2019-08-11.

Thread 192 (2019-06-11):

Úprava držáku kotvy magnetu

ChroustJan, 2019-06-11:
Je potřeba vytvořit nový díl, který bude držet kovovou část (žlutě ohraničený díl), která se chytá na magnet na střeše auta. Je potřeba, aby se aktuální umístění kovové části posunulo o svůj celý průměr dozadu do bíle vyznačené oblasti (bude nově začínat tam kde aktuální končí). Viz znázornění na fotce.

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

Díl by měl vzniknout úpravou držáku předního kolečka.

roman-dvorak, 2019-06-11:
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

Při vytváření tohoto dílu lze vycházet z 888_2003, který byl umístěn na stejném místě. Popřípadě ho rovnou upravit.
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

ChroustJan, 2019-06-12:
Je důležité, aby ten držák byl trochu vysunutý, aby nedošlo ke kolizi s tím modrým dílem držící motor. Podle mě bude určitě stačit 1cm pod tu fialovou desku UAV. Možná i 5mm.

kaklik, 2019-06-24:
Současný držák 888_2003 je vysunutý příliš a zbytečně zvedá vírník nad magnet.

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

ChroustJan, 2019-07-02:
Je potřeba provést opravu dílu. Skrz celý materiál je šestihranný otvor. Matice propadá.

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

kaklik, 2019-07-13:
Na opraveném dílu kotva magnetu drží.

Closed 2019-07-13.

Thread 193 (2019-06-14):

Sestava rotorové hlavy 2300

kaklik, 2019-06-14:
V [sestavě rotorové hlavy](https://github.com/ThunderFly-aerospace/TF-G1/blob/master/STL/drawings/666_2300.stl)  je potřeba opravit tyto nedokonalosti:

- [x] Plech kování rotorového listu je v sestavě pouze ze spodní strany reálně má být z  obou stran listu
- [x] listy včetně kování jsou v sestavě špatně "nasezeny na rotorový domek".
- [x] listy nemají být v rovině ale při rotaci tvoří kužel se vzepětím cca 3 stupně.
- [ ] V sestavě chybí znázornění motoru(válec) a [pastorku řemenice](https://github.com/ThunderFly-aerospace/TF-G1/blob/master/STL/prerotator_pulley_motor.stl)
- [ ] Bylo by vhodné doplnit i gumové dorazy (kvádry) pod kování listů

kaklik, 2019-06-16:
[Pastorek řemenice na motoru ](https://github.com/ThunderFly-aerospace/TF-G1/blob/master/STL/prerotator_pulley_motor.stl)

Patří takhle:

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

Pod ním je [motor](https://www.rc-zoom.cz/ray-g2-stridavy-motor-c3548-900/), který navrhuji zjednodušit na válec o průměru 35mm  a výšce 48mm.

kaklik, 2019-06-17:
Naklonil jsem rotorové listy podle parametru [rotor_blade_AOA](https://github.com/ThunderFly-aerospace/TF-G1/blob/44e428676b9d4ba5ae5c1bf5843792632330ace5/Parameters.scad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)

Protože jsem si myslel, že to vyřeší chybu renderování listů při zmáčknutí F6.
Problém to nevyřešilo a listy stále nejsou ve vyrenderované sestavě vidět.

Nicméně jsem si všiml, že v modelu jsou duplicitně definovány parametry delka_listu a  sirka_listu, které nejspíše odpovídají parametrům rotor_blade_length a rotor_blade_depth v [konfiguračním souboru](https://github.com/ThunderFly-aerospace/TF-G1/blob/44e428676b9d4ba5ae5c1bf5843792632330ace5/Parameters.scad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).

Parametr "uchytna_cast" pravděpodobně je také z něčeho odvozený.

kaklik, 2019-06-17:
Taky jsem si všiml, že nově není rotorová hlava konzistentně nakloněná ve stejném úhlu jako deska podní.  V minulé verzi sestavy to bylo.  Je  nějaký důvod proč tahle vlastnost byla odstraněna?

Ještě v[ téhle verzi](https://github.com/ThunderFly-aerospace/TF-G1/blob/658d5fda9a4f3f4b3a37798e6f471bce17518e63/STL/drawings/666_2300.stl) ten náklon byl.

kaklik, 2019-06-21:
Pro tu tvorbu sestav by to chtělo vymyslet nějaký udržitelnější postup. Protože jak jsem se díval, tak je to plné čísel o kterých není jasné, kde se vzaly.

Navíc některé záležitosti pak nesedí dobře (protože se zřejmě nepočítají z parametrů).  Tady je například osa rotace hlavy.

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

kaklik, 2019-08-07:
Myslím, že tohle můžeme pro současnou konstrukci rotorové hlavy považovat za vyřešené. Další zlepšení bude potřeba až s novou generací rotorové hlavy.

Closed 2019-08-07.

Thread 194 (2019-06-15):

Úprava ocasních ploch

roman-dvorak, 2019-06-15:
Existující řešení ocasních ploch ve tvaru písmene H má řadu problémů, které by vyřešily ocasní plochy ve tvaru písmene A. Pro toto issue lze vycházet z existujícího modelu ocasních ploch. Toto řešení by mělo zvětšit pevnost ocasu a snížit možnost střetu s rotorem.

Nově bude ocas přidělán pomocí dvojice trubek (D=10mm), které budou vycházet z podložky vírníku.

Servo bude nahrazeno servem  (BMS-115HV) s otvory pro boční přidělání. Tato úprava má hlavní přínos v tom, že bude podstatně snazší servo demontovat a vyměnit. Rozměry tohoto serva mám oměřené.

Ocasní plochy by se měly skádat ze dvou částí, které budou na horní straně vzájemně sešroubované.

Tvar ploch  by měl vycházet z [existujícího modelu](https://github.com/ThunderFly-aerospace/TF-G1/blob/master/src/666_1028.scad).

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

kaklik, 2019-06-18:
Issue, které se zabývá uchycením serv v ocasních plochách je zde: https://github.com/ThunderFly-aerospace/TF-G1/issues/120

alcamrkvicka, 2019-06-24:
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

Cast pro zapusteni je navrzena na sroub M3 ISO7380

roman-dvorak, 2019-08-13:
Protože pro přidělání ocasních ploch budou použity uhlíkové trubky s vnějším průměrem 10 mm a musí být skrze ně provlečeny alespoň 3 dráty k servům, tak není možné trubku provrtat a sešroubovat. Při tomto postupu navíc hrozí výrazné oslabení pevnosti trubky a její následné zničení vlhkostí.

Proto byl vymyšlen postup, že na konci trubky bude takový vytištěný "adaptér", který se na trubku nalepí a sešroubuje se zbytkem směrovky.

Je potřeba aby tento adaptér odpovídal profilu křídla. Ze zadní strany by měl mít otvor na provlečení kabelů. Jeho spojení se zbytkem směrovky by bylo provedeno sešroubováním. Jako nejlepší místo na sešroubování mi připadá umístit šrouby pod a nad připevňovací trubku, kdy by se šroub zastrčil ze předu. V hlavním díle směrovky by byly díry na kapsy pro matky a díry pro šrouby.

Trochu načrtnuté je to zde. Pokud jsou nějaké nejasnosti, ptej se na cokoliv :

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

kaklik, 2019-08-13:
Já bych to asi raději viděl tak, aby se ten díl šrouboval ke směrovce zboku, nikoli zepředu. Část toho dílu by tak stále byla permenentně součástí směrovky. Domnívám se, že se to tak bude i lépe tisknout.

V jaké poloze se vůbec bude tisknout tahle nová směrovka?   Moje představa je, že bude spodní hranou profilu stát na podložce.
Aby ale v takovém případě mohl být vytištěn otvor pro pohyblivou část směrovky, tak směrovka musí být zkosená.

roman-dvorak, 2019-08-19:
Já jsem totiž myslel, že se to bude tisknout náběžnou hranou dolů. Je blbé, že pak ta hrana není hezká. Aby se to tisklo na stoajto, tak ta zkosená hrana bude muset být dost zkosená. To mi skolo vychází tam vymodelovat podpory ručně a nahoře udělat most. Ta podpora by měla stále tvar airfolu té směrovky jen by tam bylo dutá komora.

A z toho předpokladu, že se to bude tisknout na náběžnou hranu, tak jsem zvolil šrouby takto umístěné. Při bočním umístění šroubů se bojím toho, aby kvůli šroubům se směrovka zbytečně neztlusťovala.

kaklik, 2019-08-19:
Ten tisk na náběžné hraně není optimální. Vyžaduje v modelu vymodelovaný brim, který je pak třeba odřezávat.
Použití vymodelovaných podpor místo úkosu je dobrý nápad.

Na šrouby tam může být boule, která může být i součástí boule pro trubku.

taury55, 2019-08-23:
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

Ty trubky, na kterých budou plochy uchecny mají jaký rozestup?

roman-dvorak, 2019-09-01:
V modelu je několik nových problémů:

 * Tloušťka stěny profilu je moc velká. Dříve pro to existoval parametr, který tuto šířku definoval.
 * Chybějící podpora pro tisk místa pro adaptér. Bylo by vhodné namodelovat vlastní podporu než to nechat na slieru nebo celý airfoir
 * Díra na servo je moc nízká
 * Příčka pro připevnění serva je moc blízko vnitřnímu kraji
 * Pozice otvoru je špatná - páka serva vychází na spodní část směrovky

roman-dvorak, 2019-09-02:
Pokud jsou předchozí body nesrozumitelné, tak tady je rozepisuji:

1. to je asi jasné

2. Servo se do otvoru nevejde na výšku. Chybí tam asi 1 mm. Ale i pokud se to rozšíří o 1 mm na některou stranu, tak díry pro připevnění serva jsou ve špatné výšce.
Na obrázku je nakreslen rozměr, kterým myslím výšku otvoru
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

3. Uvnitř otvoru pro servo jsou 2 "stěny" za které má být servo přišroubované. Připadá mi, že jsou úplně uprostřed. Je potřeba je posunout trošku k vnější straně směrovky. Důvod, tohoto posunu je, že nyní servo bude velmi vyčuhovat ven z profilu
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

4. Pokud bude servo v součastném otvoru směrem dolu, bude to vycházet tak, že táhlo bude na spodním okraji pohyblivé části směrovky. Bude to vycházet tak, že kabel od serva bude vždy na vzdálenější straně od tyče. Ale to se asi musí vyřešit šikovně udělanou cestičkou.

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

roman-dvorak, 2019-09-07:
Po vytištění směrovek se ukázalo několik problémů.

 - [ ] Výplň v horní části
 - [ ] Silnější horizontální stěny v okolí podpor
 - [ ] Zaslepit otvor pro osu pohyblivé části

1) V části, kde je zešikmení pro sešroubování dvou polovin je problém, že neni namodelovaný infill. Infill je potřeba mít namodelovaný až do konce. Pokud se to tiskne bez infillu tak tam díky velkému zšikmení nedrží vrstvy po hromadě a je to velmi měkké.

2) V místech, kde jsou domodelované podpory (tedy v místě pohyblivé části a v místě, kam patří adaptér na tyč) jsou velmi tenké horní a spodní stěny. V těchto místech bych to navrhoval zesílit (alespoň na 2 - 3 vrstvy). Protože situace je taková, přemostění není moc kvalitní - jsou v něm velké mezery. A snadno se trhá. To i při vyřezávání podpor.
Další vhodná úprava by bylo nad  a pod podporami udělat droubou mezeru, aby zde plast nebyl tak doře spojen.

3) Ve spodní části směrovky nemít díru pro osu směrovky až veskrz. Nechat pod ní pár vrstev (více než 1) Díky tomu se nebude muset zalepovat tavným lepidlem. Nahoře tyčky budo zajištěny tím, jak se směrovky sešroubují.

roman-dvorak, 2019-09-07:
Směrovka pro nový model je zřejmě dost malá. Je potřeba zvětšit její plochu. Vzhledem k tomu, že je využit celý tiskový prostor, musí se model rozdělit na více částí. Zároveň by se tím dal vyřesit problém potřeby modelovat podpory.

Představoval, bych si to tak, že se to rozdělí na 3 části. Spodní část, prostřední část - část, kde je pohyblivá část směrovky a třetí část by byl horní zbytek. Tyto 3 části by se následně slepily. popř. sešroubovaly.

Díky tomu je možné zvětšit výšku střední části do tiskárny a zároveň by bylo možné zvětšit hloubku profilu.

roman-dvorak, 2019-10-06:
Dneska jsme složili novou verzi směrovky. Ukázalo se několik problémů.

- [ ]  Nelze složit pohyblivá část směrovky s pevnou částí. Problém je, že díry pro tyčku jsou moc blízko konci výřezu pro pohyblivou část.
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

- [ ] Servo přesunout tak, aby kabel vedl rovnou do tyče. Nový prodloužený profil to dovoluje. Přinese to výrazně rychlejší skládání.
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

- [ ] Použít jiný způsob modelování tohoto křídla. Jak to funguje, jsem se snažil popsat na [wiki](https://github.com/ThunderFly-aerospace/TF-G1/wiki/Modelov%C3%A1n%C3%AD-k%C5%99%C3%ADdel) Zřejmě to stále není dostačující. Takže jestli to z toho nechápeš, prosím napiš, pokusím se Ti doupřesnit, jak je to myšleno.

- [ ] Všechno má strašně silné stěny. Stačil by jeden perimetr - pokud vyřešíš předchozí bod, tak toto nebudeš muset řešit. Protože to pak vyřeší slicer.

roman-dvorak, 2019-10-13:
- [ ]  Infill je dost hustý. Navrhuji zkusit vzdálenost výztuh nastavit na nějkých cca 130 % z aktuální hodnoty

- [ ] Odebrat díry pro vyztužení pomocí uhlíkových tyček. Zároveň tam pak nemusí bý ty plné výplně, které mají tyčky držet. Konstrukce se tím znovu odlehčí.

- [ ]  Pozice otvoru na servo je OK. Servo umístit blíže k vnější straně. Pokud servo vložím ze strany, kde je přepážka blíže ven, tak by to chtělo servo zapustit o 1 mm hlouběji.  Příčku, ketrá podepírá serrvo udělat tlustší (až na druhou stranu k vnější stěně profilu. Pro připevnění serva by se použily samořezné šrouby. Vzdálenost otvorů pro šrouby by měla být 28 mm. Průměr této díry ještě upřesním.

- [ ] Na vnější straně směrovky zrušit díru pro servo. Servo se tam vloží i přišroubuje z vnitřní strany. Tato strana by měla být hladká a voděo odolná.

- [ ] Pro minimalizaci možnosti vniknutí vody do serva by servo mělo být natočeno směrem dolů.

- [ ] Na spodním dílu směrovky je díra pro osu směrovky vyvedena až ven. Je potřeba udělat její zaslepení. Zrychlí to montáž směrovky.a zjednoduší výrobní postup.

- [ ] Páka má stejný přesah i rozteč montážních děr jako její menší verze na staré směrovce. Takže tuto pozici táhla je nejlepší vzít odsud. Podle měření je tento přesat 5.5 mm od první montážní díry.

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

- [ ] Na jednom středním dílu směrovky chybí otvory pro připevnění držáku na tyč.

- [ ]  Odstranit tuto dílu na obrázku pod servem. Zřejmě nějaký pozůstatek po tunelu..

kaklik, 2019-10-22:
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

- [ ] šrouby adaptéru nesedí proti dírám ve směrovce
- [ ] servo je ve výklenku ze stran a zespodu hodně na těsno a je ho tam potřeba násilně vtlačit
- [ ] adaptér nepřechází plynule na plochu směrovky ale vzniká tam zub

roman-dvorak, 2019-10-28:
V servu je potřeba udělat úpravu, aby bylo možné osu směrovky snadno vytáhnout. Toto lze vyřešit odstraněním (snížením) kostky v okolí osy

roman-dvorak, 2019-11-07:
@taury55 snažím se dostat směrovku do celkové sestavy vírníku. Jak nebyly dobře pochopeny připravené parametry, tak nefungoval původní výpočet vzdálenosti tyčí, na kterých je směrovka přidělaná.

Teď jsem se snažil tento výpočet předělat tak, aby to sedělo na novou směrovku. Aby mi to sedělo, tak  k výpočtu musím přičítat nějakou divnou konstantu, aby to sedělo správně. Vidět je to např zde:

https://github.com/ThunderFly-aerospace/TF-G1/blob/improved_suspension/parameters.scad#L367

Nešlo by to nějak vyřešit?

taury55, 2019-11-11:
@roman-dvorak Dostal jsem se k tomu až teď, ale ta proměnná tail_pipe_distance je tam naprosto přebytečná a v celém 666_1028.scad není použita.

Closed 2019-11-03.

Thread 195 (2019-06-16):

Úchyt zadního kolečka na nápravnici

ChroustJan, 2019-06-16:
Pro testy na střeše potřebujeme udělat nový úchytný díl pro zadní kolečka. Díl by mohl vypadat následovně:
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

Díl přijde přidělat na zadní nápravnici o průměru 25mm. Stažení na tuto trubku by mělo být provedeno pomocí čtveřice šroubů M3. Do dílu následně přijde trubka o průměru 10mm na jejím druhém konci bude kolečko.

Není nutné tvořit díl označený číslem 2. Je možné mít proti sobě dva dílce 3.

alcamrkvicka, 2019-06-23:
888_2010
4 otvory jsou udelane na srouby M3x20, mezera mezi 2 castmi je 3 mm, je to tak ok?
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

roman-dvorak, 2019-06-23:
Tento díl mi příjde až moc zbytečně masivní. Navrhuji ho proto udělat tenčí
(a zároveň lehčí). Upevňovací šrouby dát max 1 cm od hlavní tyče. Na
straně, kam se vkládá tenčí trubka, tak udělat nějaký výčnělek nebo tento
díl udělat trochu oválný.

Myslím, že tento problém vychází z původního nákresu, který není nakreslen
úplně v měřítku.

[image: 20190623_183742.jpg]
(tento nákres také není 100 % v měřítku ale lépe popisuje poměr hlavní tyče
a sílu tištěných dílů.

tyto dvě části můžou být namodelovány v jednom souboru jako 2 moduly.

ne 23. 6. 2019 v 15:49 odesílatel Alena Mrkvičková <notifications@github.com>
napsal:

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

alcamrkvicka, 2019-06-23:
Ztenceno a upraveno do protahlejsiho tvaru...
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

ChroustJan, 2019-06-24:
Já to kreslil hodně zjednodušeně, aby to bylo jednoduché. Tento díl se mi samozřejmě líbí víc.

kaklik, 2019-06-24:
V modelu jsou [špatně užity parametry průměrů trubek](https://github.com/ThunderFly-aerospace/TF-G1/blob/81cb60f85d13ef3aa27e16925e3a3aaa7429a690/src/888_2010.scad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). @ChroustJan  sice v zadání napsal průměry 10 a 25mm. To ovšem pro model není pravda a je potřeba použít [tyto parametry ](https://github.com/ThunderFly-aerospace/TF-G1/blob/81cb60f85d13ef3aa27e16925e3a3aaa7429a690/Parameters.scad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)

roman-dvorak, 2019-07-01:
Při přimontování dílu byl zjištěn problém s tolerancemi ve velikosti parametru na 10 mm trubku. Trubka byla v tomto dílu volná.

Díl se zdá pro tento účel použitelný.

ChroustJan, 2019-07-02:
Je potřeba posunout šroub držící trubku o síle 10mm do středu dílu. Viz obrázek. Takto dochází k vrtání do trubky na jejím okraji.
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

alcamrkvicka, 2019-07-02:
Dira je presunuta doprostred.

kaklik, 2019-07-02:
@ChroustJan  issue se uzavírá až když se otestuje jeho vyřešení. Do té doby je Resolved.

kaklik, 2019-07-05:
Nový úchyt funguje.

Closed 2019-07-05.

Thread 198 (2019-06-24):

Díl 888_1101 - úklid

Elizaa62, 2019-06-24:
Prosím autora o upravení kódu v dílu 888_1101!

Omlouvám se, ale nevím, co mají znázorňovat moduly "efsm_12 apod." Dále nevím z čeho přesně se skládá stl soubor dílu 888_1101.scad - prosím v kódu vyznačit.

Dále se v kódu používají čísla, jejichž původ je neznámý, takže též prosím o vysvětlení.

Děkuji :)

roman-dvorak, 2019-06-24:
Na tomto dílu právě pracuji. Až bude dokončen, vše toto spravím. Je to nová varianta rotorové hlavy #169

Jinak EFSM-12: https://www.igus.cz/info/spherical-bearings-efsm

kaklik, 2019-06-24:
@roman-dvorak  Možná jen vysvětlím k čemu je to potřeba.
Aby mohlo být uzavřeno issue #193, tak je potřeba, aby rotorová hlava poskytovala některé náležitosti.
Například musí být jasné, kde má být umístěn motor prerotátoru (jeho imitace) a jak mají být nakloněny listy s řemenicí.
Cílem je, aby se nejasné číselné konstanty nešířily do dalších modelů.

roman-dvorak, 2019-06-26:
@Elizaa62  Já tady ale netuším, kde se bere tento posuv (těch 17.5 mm). Má to nějaký vetší význam nebo je to pouze posunutí od osy toho dílu? I rozteče těch děr pro přišroubování na trubku by chtělo definovat nějakým parametrem.

https://github.com/ThunderFly-aerospace/TF-G1/blob/1b70f4693953745a9728b779062dc351a7d923a0/src/888_1015.scad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

Sestavu [888_1101](https://github.com/ThunderFly-aerospace/TF-G1/blob/master/src/888_1101.scad) jsem přeuspořádal tak, aby to odpovidalo umisteni oproti konci svisle trubky. Ale je tam stále těch 17.5 mm nastaveno na pevno. V budoucnu by to mohlo dělat obdobný problém jako tyto mé konstanty.

Umisteni motoru ješte vytvořím jako funkci. Také to zkusím napočítat oproti konci trubky.

Jinak navrhuji vytvořit parametry, které budou definovat rotaci rotoru (a všech jeho častí), protože to může vypadat zajímavěji na různých datech pro grafika.

Vzhledem k tomu, že se vše rotuje kolem kulového čepu, tak navrhuji, že bude existovat funkce, která vrátí polohu čepu oproti konci trubky. A následně všechny další díly budou vztažené a rotované k tomuto bodu.

roman-dvorak, 2019-06-26:
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

Elizaa62, 2019-06-27:
Rozměr 17.5 značí posuv děr od osy. Je to čtvrtina rozměru 70 (nyní parametr "rotor_head_width" = 70). V kódu jsem to opravila na width/4.

Elizaa62, 2019-06-27:
V dílu 888_1101 chybí naklonění.

Elizaa62, 2019-06-27:
Je super, že je v dílu uveden model prerotátoru, ale do sestavy rotorové hlavy 666_2300 potřebuji vložit model pastorku řemenice.. jenže díl 888_1020  je od osy posunut na nějakou pozici a já nemůžu najít v kódu hodnotu o kterou je díl posunutý... Hodnotu potřebuji ke správnému umístění pastorku řemenice.

roman-dvorak, 2019-06-27:
@Elizaa62 upravil jsem tu Tvou sestavu. Zkus se na to podívat.

roman-dvorak, 2019-07-01:
@Elizaa62  Myslíš, že je toto issue dokončené? Nebo se po mne vyžaduje ještě nějaká úprava?

kaklik, 2019-08-06:
@Elizaa62  ping :)

kaklik, 2019-08-07:
@Elizaa62 Říká, že je to vyřešeno.

Closed 2019-08-07.

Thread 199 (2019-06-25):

Doplnit sestavu kolečka o vidlici 888_2103

kaklik, 2019-06-25:
Sestavu kolečka by bylo potřeba doplnit o vidlici 888_1027. Rozměry vidlice je potřeba nastavit tak, aby ke kolečku pasovala. Parametry vidlice by proto měly vycházet z rozměrů kolečka v souboru parameters.scad

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

alcamrkvicka, 2019-06-25:
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
 jak velka mezera ma mezi vidlici a koleckem byt?

kaklik, 2019-06-25:
Jestli myslíš z boku kolečka, tak žádná. Tam stačí na tloušťku té obruby vložek.
Také jsem si všiml, že ty vložky v sestavě nejsou možná úplně správně zapuštěny v kolečku po úpravách jejich délky.

Mezera mezi běhounem kolečka a zaoblenou částí vidlice stačí malá třeba 10mm. Ale do tohoto směru může být vidlice klidně delší, aby ji bylo možné uchytit za delší část trubky. Horním limitem je pak určitě tiskový rozměr 150mm.

kaklik, 2019-06-27:
Dalším požadavkem na vidlici je, aby využívala šrouby o nějaké existující délce. Pokud je to možné, tak například M4x50 nebo 55mm.

roman-dvorak, 2019-07-05:
Je potřeba upravit sestavu kolečka tak, aby poloha jednotlivých dílů byla nastavena pomocí odpovídajících parametrů a zkontrolovat jejich správnost.

Do vidlice je potřeba použít šroub M4x55. Teď to vychází na délku šroubu M4x60 (který se moc nevyrábí). To lze vyřešit tak, že se z vložky ložiska odstraní vnější lem (viz: https://github.com/ThunderFly-aerospace/TF-G1/issues/191#issuecomment-508866092 ) a o dvojnásobek jeho tloušťky se zúží vidlice. Pak je potřeba ohlídat správné zapuštění matic (a hlavy šroubu) do vidlice na délku šroubu M4x55.

roman-dvorak, 2019-07-06:
Druhá část vidlice - třmen pro šroub není namodelován s použitím stejných parametrů.

roman-dvorak, 2019-07-07:
Zaktualizovány rozměry vidlice, upraveny připevňovací body, více zapuštěny matice pro prošroubování tyče, Délka šroubu napočínána pro M4x55 DIN 912.

Closed 2019-07-09.

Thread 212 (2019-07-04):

Připravit rozdvojku pro GPS a safety switch na CUAV V5+ autopilota

roman-dvorak, 2019-07-04:
CUAV V5+ autopilot má sloučený konektor pro GPS, safety tlačítko, Safety LEDku a pípák. Z konstrukčních důvodů by bylo vhodné vyvést další safety tlačítko mimo GPS.

Nejsnazší způsob je na dodaný propojovací kabel paraelně připájet drátky s tlačítkem. Pípák může zůstat ten, co je v GPS.

Je možné využít dodané safety switch, které má dokonce montážní otvory a LED v tlačítku.
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

Rozteč montážních otvorů je 19 mm, střed děr od okraje PCB je 5 mm a díry jsou pro M3 šruby.

Pinout konektoru na autopilotu je následující:
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

kaklik, 2019-07-15:
Vyřešeno vyrobením nového kabelu ke GPS s piny oddělenými pro safety switch.

Closed 2019-07-15.

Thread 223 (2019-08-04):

Nová konstrukce nosné podložky

ChroustJan, 2019-08-04:
Při zvětšování nosné podložky dochází k problému nutnosti dělení dílce na tisknutelné části. Tento proces není příliš jednoduchý. Stávající podložka se také tiskla kolem 80h. Při vývoji a testech je potřeba co nejsnáze měnit rozložení vnitřní výbavy vírníku. Přibývá nová elektronika, nebo je potřeba posunout například baterie kvůli těžišti.

Nová konstrukce má pouze dva hlavní dílce:
- tuhý středový trup skrz který vede dvojice uhlíkových trubek (v nákresech 1)
- okrajový dílec skrz který vede jedna uhlíková trubka, dílec také obsahuje drážku pro uchycení krytu vírníku jako tomu bylo u současného řešení ( v nákresech 2)

Nákres ze shora:
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

Konstrukce umožňuje zachovat stávající díl předního motoru. Pouze bude potřebovat upravit uchycení na dvojici trubek. Plánovaný ocas se také nemění. Pouze bude vytvořen dílec pro uchycení dvojice trubek z ocasu na dvojici trubek rámu vírníku. Konstrukce zakrytování vírníku bude také zachována. Pouze bude jiné rozložení otvorů pro úchytné šrouby.

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

Náčrtek dílce hlavního nosného trupu. V rámci iterací bylo rozhodnuto, že se ocas nebude chytat na nosné trubky, ale na pomocné boční. Viz. první obrázek pohledu na vírník z vrchu.

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

Podrobnější rozkreslení dílce 1 a 2:

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

Dílec 1:

- jeho délka by měla být parametricky rostoucí. Maximální délka je omezená velikostí tiskárny.

- skrz celý díl procházejí dvě trubky (aktuálně o průměru 10mm) v jejich ose je vždy otvor pro šrouby M3, aby bylo možné trubku prošroubovat s tištěným dílem. Z obou stran otvoru musí být počítáno s tvarem pro umístění matice.

- po cca 50 mm možnost vložení dvojice trubek (aktuálně průměr 10mm) kolmých na hlavní nosné. Možnost jejich prošroubování šroubem M3, matice zas zapustit z obou stran dílce.

- v ose šroubů pro prošroubování hlavních trubek dát ještě kapsy pro matici M4, aby bylo možné z boku dílce uchytávat příslušenství. Uprostřed otvor pro šroub M4 se zapuštěnou maticí na obou stranách.

Dílec 2:

-obsahuje po své délce drážku pro kryt vírníku s kapsami pro M3 matici.

- po své délce má otvor na trubku (aktuálně 10mm průměr), zas by mělo být myšleno na možnost prošroubování s tištěným dílcem.

- otvory z boku pro pomocné trubky (aktuální průměr 10mm) s možností jejich prošroubování.

Ukázka možností uchycení příslušenství v konstrukci:

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

Varianta 1:

- dvojitý dílec mezi dílem 1 a 2. Při povolení jeho šroubů je možné popojíždět dopředu dozadu, dle potřeby. Do tohoto dílce mohou být umístěny různé úchyty dle potřeby. Tento díl je uvažován například pro uchycení baterií.

Varianta 2:

- uchycení na hlavní trub z boku na matici M4, která je v kapse trupu. Možné využit například pro uchycení rotoru. Pokud se díl udělá dostatečně široký, je možné následné vyztužení trubkou kolmou vůči trupu. Dílec se na danou trubku pouze nasune. Nebude potřeba vrtání a lepení.

Varianta 3:

- pomocí šroubu M4 skrz trup. Trup má standardně tento otvor se zapuštěnou maticí s obou stran. Je možné umisťovat držák jak zespodu tak ze shora.

Náčrtek možného uchycení zadní nápravy:
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

Toto uchycení by mělo umožňovat snadnou demontáže celé zadní nápravy pro servis. Může jí držet třeba 4-8 šroubů. Základní uchycení je na hlavní trub s možností využití využití vedlejších trubek.

roman-dvorak, 2019-09-16:
- [ ] Sjednotit rozměry děr (a příslušných matek) skrze nosník
- [ ] Do sestavy přidat značky pro jednoduché určení dílů
- [ ] Odebrat podpory pro tisk univerzální drážky.

roman-dvorak, 2019-09-23:
Nosník se zdá použitelný. Další problémy budou mít vlastní issue.

Closed 2019-09-23.

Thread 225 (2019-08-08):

Tisknutelný kloubový spoj rotorové hlavy

kaklik, 2019-08-08:
Současná tisknutelná rotorová deska, viditelná na následujícím obrázku funguje relativně dobře.
Díl se nyní naklání volně obou osách (podélně-pitch i příčně-roll). Problém je dost vysoká volnost okolo vertikální - Yaw osy.

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

Existují dva možné přístupy k tomuto problému.

1. Nebo upravit tvarový kloub bránící protočení hlavy, tak aby neměl tak velkou vůli a nebo když to nebude možné tak
2. Opustit hlavu v provedení spindle head, která má pro 3D tisk výhodnou skladbu a navíc umožňuje teoreticky let na zádech a nahradit tuto konstrukci klasickým uspořádáním [offset gimbal head](http://www.msgyro.com/photos/Bensen_Gimbal_Head_Hub_Bar_and_Head_Plates_504x379.jpg)

slimonslimon, 2019-08-08:
mám v hlavě návrh kolem toho kulového kloubu udělat tisknutý kardanův kloub.

ten kulový kloub umístit na vyvýšenou plošinku, která by měla v jedné ose očka přesně ve výšce kloubu, pak druhý díl, který by to obepínal zvenku (mohl by mít shora plošku se zářezem pro tyčku, což by mu zvýšilo pevnost) a třetí díl (vlastní deska s prerotátorem) by měla dvě očka smerem dolů a obepínala by s offsetem ten prostřední díl - kromě oček by s tohoto dílu musel být vytištěn ještě krček kolem osyčky, který by zajišťoval stažení horního dílu proti kulovému kloubu

slimonslimon, 2019-08-08:
přes kardanův kloub by neměli jít v podstatě žádné síly, krom kompenzace yaw

slimonslimon, 2019-08-08:
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

kaklik, 2019-08-08:
Jo, tohle hybridní řešení se mi docela líbí. Pokud to navíc cené nevyjde moc masivní, tak v tom nevidím problém.

Pokud to správně chápu, tak ty otočné části ani nemusí být spojeny osou ale stačila by jen břitová vazba,  Podobně jako to máme na [vyvažovacím přípravku](https://github.com/ThunderFly-aerospace/TF-G1/blob/master/STL/manufacturing_helpers/888_1009.stl).

slimonslimon, 2019-08-08:
břitová vazba zní zajimavě, bylo by to jednodušší na složení a asi i kreslení, akorát nevím jak dobře drží proti rotaci (yaw).

kaklik, 2019-08-09:
> břitová vazba zní zajimavě, bylo by to jednodušší na složení a asi i kreslení, akorát nevím jak dobře drží proti rotaci (yaw).

Tak bude to držet tak moc, dokud se ty břity neulomí. Ovšem vzhledem k tomu, že tady nejde úplně o nutnost malého odporu spoje, tak by břity ve skutečnosti mohly mít i poměrně nízký rozsah úhlů. Pak by pevnost vazby nebyla dána tolik pevností břitu, ale pevností kulového ložiska proti vytažení kuličky. (klín břitového spoje by při krutu v ose yaw působil silou roztahující celý kulový spoj.)
Zřejmě zde bude existovat nějaké optimum pevností. Neboť je výhodnější, aby se při havárii hlava protočila a nikoliv utrhl celý rotor.

kaklik, 2019-08-19:
Kloubový spoj funguje a nyní je potřeba jej implementovat do nové verze rotorové hlavy.

Closed 2019-08-19.

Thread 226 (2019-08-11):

Oprava vnějšího průměru vložky pro šroub M4 do 8mm igus ložisek

kaklik, 2019-08-11:
Vytištěná vložka má průměr 7.3mm  potřebný průměr je 8.0mm

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

roman-dvorak, 2019-08-13:
Pro tento účel jsem vytvořil parametr nový `M8_plug_diameter`. Velikost tohoto rozměru byla změněna z `8-0.5` na `8`mm

Closed 2019-08-18.

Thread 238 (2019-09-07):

Varianta desky rotorové hlavy s kardanem

roman-dvorak, 2019-09-07:
V návaznosti na #149 #169 a #225 se ukazuje, že tisknutelná deska rotorové hlavy má několik prolémů, které by bylo možné vyřešit frézovanou deskou tak, jak tomu bylo u #169.

Problémy byly především v tom, že je těžké vytisknout dostatečně tuhou desku. Především od krčku, kudy prochází osa rotoru po táhla od serv. Další problém je, že plastová deska neodvede od motoru prerotátoru dostatek tepla a pak se plast natavuje. Čímž se zmenšuje vzdálenost řemenic a tedy napnutí řemene. Ten následně přeskakuje.

Původní řešení mělo problém, že čep, který měl držet rotor v konstrantním Yaw úhlu se vymačkal do plastu a byla tam velmi velká vůle. Proto vznikalo několik variant řešení tohoto kloubu. Následně @slimonslimon přišel s řešením, které se zdá jako funkční. Použití obdoby kardanova kloubu. V YAW je zde vemi malá vůle. Vytištěné řešení má zmíněné problémy.

Je varianta, že deska by byla stále frézovaná z 5 mm duralové desky AW7075 a kardan by byl vytištěný a přišroubovaný k této desce. V desce by byly z horní strany dva M3 šrouby a v kardanu (v nejvyšší části) by byla kapsa na matky.  Tím by se docílilo dobré tuhosti dílu a zároveň využití kardanu pro účely omezení rozsahů pohybu a úhlů.

Deska by mohla vypadat nějak takto:
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

Ze spodní a z hodní strany by byly 2 soustružené díly, které by vymezovali správnou vzdálenost mezi deskou, kulovým ložiskem a ložisky rotorové hlavy.

Desku bude možné ještě podstatně více odlehčit.

slimonslimon, 2019-09-08:
nakrelsit plastový díl který by se na tu desku přišrouboval je triviální - defacto by to byl díl který vznik pro test kardanu (bez čísla v nějaké kardanové větvi). Akorát by měl uprsotřed dáru na ty soustružené díly.

trochu otázka je, jak naložit s výškou toho krčku.

slimonslimon, 2019-09-08:
mimochodem, u současného řešení je také duralová deska - jak je vyřešeno usazení na to kulové ložisko?

Defacto by se pro potřebu testu dala současná deska upravit...

roman-dvorak, 2019-09-08:
Tam není žádný krček. Deska leží skoro přímo na kulovém ložisku. Je tam pouze vytištěná podložka/vložka ložiska, která má tloušťku něco okolo 0.5 mm. Nad deskou jsou jen okolo osy 2 podložky a hned ložiska.

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

slimonslimon, 2019-09-09:
Ještě další otázka : V #169 je zmíněna varianta z duralového plechu - to je slepá vývojová větev?

roman-dvorak, 2019-09-09:
Na obrázku v mém minulém komentáři je právě ten plech, který má výkres v #169. Náhrada za tisknutelný díl se zdála v té době vhodná z důvodu, že to umíme snáze vyrobit.

Následně pak přišlo několik variant tisknutelné hlavy a konečně ta tvá se zdála použitelná. Při namontování na vírník a následných testech se objevilo několik nových problémů.

Takže já jsem velmi silně pro tyto dvě řešení spojit a vzít z nich ty dobré části.. :) Jako základ frézovaný plech a jako kloub použít kardan.

roman-dvorak, 2019-09-16:
O víkendu jsem se stavil novou verzi rotorové hlavy. Konstrkce je zajímavá a docela dost pevná. Problém je v uchycený tyčí do podložky #241.

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

Toto řešení má několik problémů:

Snížením profilu desky je deska podstatně měkčí. Díky tomu ji velmidokážu ohnout tak, že se kolo desky dotkne. To by měl vyřešit duralový plech. Vypadá to, že výška krčku půjde snížit na minimum.

Další problém je, že nyní k tomu nelze připevit igus táhla. Důvodem je velká objímka kuličky. Objímka nyní koliduje s řemenicí či řemenem.

Pevnost v Yaw se zdá dostatečná. Ale to je pouze na základě testů v ruce.

slimonslimon, 2019-09-16:
vzhledem k tomu, že rámeček kardanu mám možnost se opřít při zkoucení o podpůrné okraje, tak to asi rozlámat jen tak nepůjde, ale nechme se překvapit.

nabízí se varianta, že by na duralovou desku byly přidělány tisknuté prvky na přidělání táhel - to by se dalo zkombinovat s tisknutými zuby a boky kardanu.
Duralový plech by pak nemusel být frézovaný, mohl by být pouze vrtaný o konstantní šířce- zezdola by k němu byl přišroubován tištěný díl.

roman-dvorak, 2019-09-16:
Jojo, o tom jsem také přemýšlel, že by to táhlo bylo přidělané přes nějaký vytištěný díl. Že by tato tištěná "kostka" byla přišroubovaná stejným způsobem jako kardan a pak by obsahovala otvor pro připevňení táhla.

Je pravda, že pro první verzi by stačil vzít duralový plech a z něj to vyvrtat. Jako jediný problém vidím s přesným vyvrtáním té díry pro osu. Aby to mělo správné tolerance. Zatím by tam nebylo řešěno odlehčení dílu atd.. Nebo jen nějak dočasně.

roman-dvorak, 2019-10-07:
- [ ] Střední díl kardanu má okolo sebe velmi velké tolerance. Důsledek toho je, že kardan má značnou volnost v yaw ose. Tolerance můžou být poloviční.

- [ ] Rohy středního dílu kardanu udělat kulaté. To by mělo zvýšit odolnost rámečku proti prasknutí a vyšší pevnost v rozích.

- [ ] Do desky kardanu vytvořit otvory pro možnost utáhnout šrouby držicí ložisko bez nutnosti demontáže celé hlavy.

kaklik, 2019-10-14:
Nová konstrukce je funkční.

Closed 2019-10-14.

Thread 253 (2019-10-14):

Tolerance vnějšího kardanu spindle head rotorové hlavy

kaklik, 2019-10-14:
- [x] Střední díl kardanu má okolo sebe velmi velké tolerance. Důsledek toho je, že kardan má značnou volnost v yaw ose. Tolerance můžou být poloviční.

_Originally posted by @roman-dvorak in https://github.com/ThunderFly-aerospace/TF-G1/issues/238#issuecomment-538888355_

roman-dvorak, 2019-10-28:
Kardan je nyní velmi tuhý! Takto nastavené tolerance jsou super.

slimonslimon, 2019-10-29:
byla to chyba v kódu, kdy horní díl měl 2x větší vůli než měl mít...

Closed 2019-10-28.

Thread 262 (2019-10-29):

Zpevnění předního kolečka

roman-dvorak, 2019-10-29:
Při testu se ukázalo, že přední kolečko #189 není dostatečně tuhé a kolečko se z dílu dokázalo vylomit.
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

Při prohlížení dílu se zjistilo, že trubička okolo osy není s ničím zpevněna. Pouze infillem. Tento problém je potřeba eliminovat několika změnami současného dílu.

- [x] Použití delšího lícovaného šroubu 8x70.
Tato změna by měla sílu rozložit na větší plochu. Ale i tak by v  dílu byla trubička, která nebude ničím pořádně vyztužena. To je potřeba vylepšit dvěmi způsoby.

- [x] Prodloužení kapsy na matku.
Kapsu na matku lícovaného šroubu by bylo vhodné udělat skrz celý díl. V orientaci zepředu dozadu.

- [x] Vyztužovací otvory u osy kolečka.
V dílu vymodelovat výztuhy od osy kolečka. Takové výztuhy mají za cíl v dílu vytvořit perimetry, které budou spojovat trubičku osy s vnějšími perimetry. To může být provedeno tak, že skze model budou vytvořeny díry (např d=1mm), které budou následně umístěny do spirály podél lícovaného šroubu.

- [ ] Změna orientace vrstev při tisku modelu. Díl by měl být namodelován tak, aby umožňoval tisk vrstev co nejblíže ideální orientaci 45 stupňů vůči ose šroubu procházejícího ložisky.

Mělo by to být uděláno tak, že následující díra bude pootočena např o 110 stupňů a o cca 3 mm výše.

- [x] Mezi prvním a druhým dílem předního podvozku (tam, kde se podvozek otáčí) je potřeba do horního dílu zapustit podložku. To má za cíl zvětšit plochu, přes kterou se přenáší síla a díky zapuštění nebude mezi díly taková mezera. A při větší síle se styčné plochy těchto dílů o sebe opřou a nebudou tolik vylamovat osu.

Tyto body jsou znázorněny na následujícím nákresu:
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
Na prvním obrázku je vidět vnitřní struktura dílu. Na druhém je pak řez při pohledu z boku.

- [x] Zarážky, které zamezují přetočení kolečka udělat širší.

kaklik, 2019-10-30:
Alternativní možností, jak držák kolečka zpevnit je udělat ho žebrovaný. Podobně, jako byl [zpevněn krček rotorové desky](https://github.com/ThunderFly-aerospace/TF-G1/blob/f3a17a0dad45fde1ed40cace4f3c18f7caf67669/STL/888_1020_plastick_neck.stl).

kaklik, 2019-11-12:
Šrouby držící horní díl předního kolečka musí mít matky až pod kapsou pro matku hlavní osy kolečka. Cílem je aby v žádné části dílu nebyly síly přenášeny tahem za vrstvy ale, tlakem.

Nejdelší M4 šrouby, které aktuálně máme jsou M4x55 mm dellší by bylo nutné koupit.

roman-dvorak, 2019-11-12:
No, aktuálně tam jsou použity šrouby M4x55.

kaklik, 2019-11-13:
Také je potřeba, aby model byl uzpůsoben na kratší páku serva. Nově bych tam dal páku 25mm.

Closed 2019-11-19.

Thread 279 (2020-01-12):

Získání translací z Slic3r při slicování do gcodu.

roman-dvorak, 2020-01-12:
Dosavadní makefile generoval pouze stl soubory. Tyto soubory se pak využívaly k tisku a využívaly se v sestavách.

U některých modelů (např tištěný rotor) by bylo vhodné mít možnost používat modifikátory k automatizování používání modifikatorů je potřeba právě AMF (více o tom v #278)

Dále by to chtělo prozkoumat, jestli je potřeba generovat i STL. Nebo jestli dokážeme STL plně nahradit s AMF. Popřípadě jak by taková konverze měla vypadat.

kaklik, 2020-01-12:
@JanKott  Podíval by ses na to?

JanKott, 2020-01-20:
Nějak nerozumim o co jde. Můžete mi to trochu rozvést?

roman-dvorak, 2020-01-20:
Jo, v tomto issue není přesně popsáno, co by bylo potřeba.

K slicování dílů používáme Slic3r. Ten byl vybrán z důvodu, že jako jediný umí nějakým způsobem pracovat s konfiguračními soubory a z přikazové řádky.

Při slicování s modelem udělá dvě zásadní věci a to to, že ho přesune v ose Z tak, aby přesně seděl na podložku a pak model vycetruje v X, Y. Tyto translace jsou neznámé.

Bylo by ideální aby se tyto informace ukládaly přimo do gcodu. Znalost této translace je potřebná třeba při výpočtu těžiště modelu z gcodu. Pokud je infill velmi řídký, tak se těžiště plného tělesa (STL/AMF) může o dost lišit oproti těžišti gcodu.

Dokud jsme používaly STL, tak jsem udělal skript, který si určil hranice STL soubory. Následně to porovnal s gcodem a podle toho odhadl všechny tři posuvy. Ale s použitím AMF to zatím neumím a je to strašně nesystémové řešení. Proto by to bylo nejlepší upravit v Slic3eru.

JanKott, 2020-01-22:
Zkusim se kouknout do zdrojáků, ale jen tak cvičně - tohle by nestačilo:

--export-gcode will center the model around the centroid point of the configured print bed (**unless the --dont-arrange option is supplied: original coordinates will be used in that case**) ?

roman-dvorak, 2020-01-22:
Ano, zarovnání okolo středu - tak to je výchozí nastavení. A tam právě vznikají ty tři neznámé transformace.

Vypnutí posuvu je také možné. Tam je však velmi slžité zajistit v modelech, že jsou umístěné nějakých 7.5 a 7.5cm mimo počátek souřadnic. A 0mm v ose Z. Naopak většina modelů se modeluje v počatku souřadnic (není to pravidlo).

Na základě těchto předpokladů právě funguje ten můj skript pro STL, který tu transformaci odhadoval. Pak je další věc, když se bude tisknout na více různých tiskárnách. Jedna má podložku 15x15, další 18x18 a pak 20x20 či více. A bylo by fajn, aby to bylo vždy ve středu. (tohle je ostatně také trochu nedořešené z pohledu generování gcodu, kde se využívá pouze jeden konfigurák pro všechny.

kaklik, 2020-01-22:
Těch konfiguráků pro tisk si dovedu představit, že bude více. Každopádně je ale nežádoucí, aby se při tisku na jiné tiskárně muselo šahat do modelu.

kaklik, 2020-02-05:
Tady je testovací příklad (AMF a STL), který vygeneruje kostku spodní stranou 100mm nad podložkou v počátku souřadnic.
Další alternativní posuvy je třeba dodatečně vyzkoušet:

[test.zip](https://github.com/ThunderFly-aerospace/TF-G1/files/4160663/test.zip)

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

JanKott, 2020-02-13:
Doplnil jsem zapicosvání posunu a rotace do gcode souboru. Na příkladu to funguje, až to zkusíte na něčem složitějším, dejte vědět.

Closed 2020-02-13.

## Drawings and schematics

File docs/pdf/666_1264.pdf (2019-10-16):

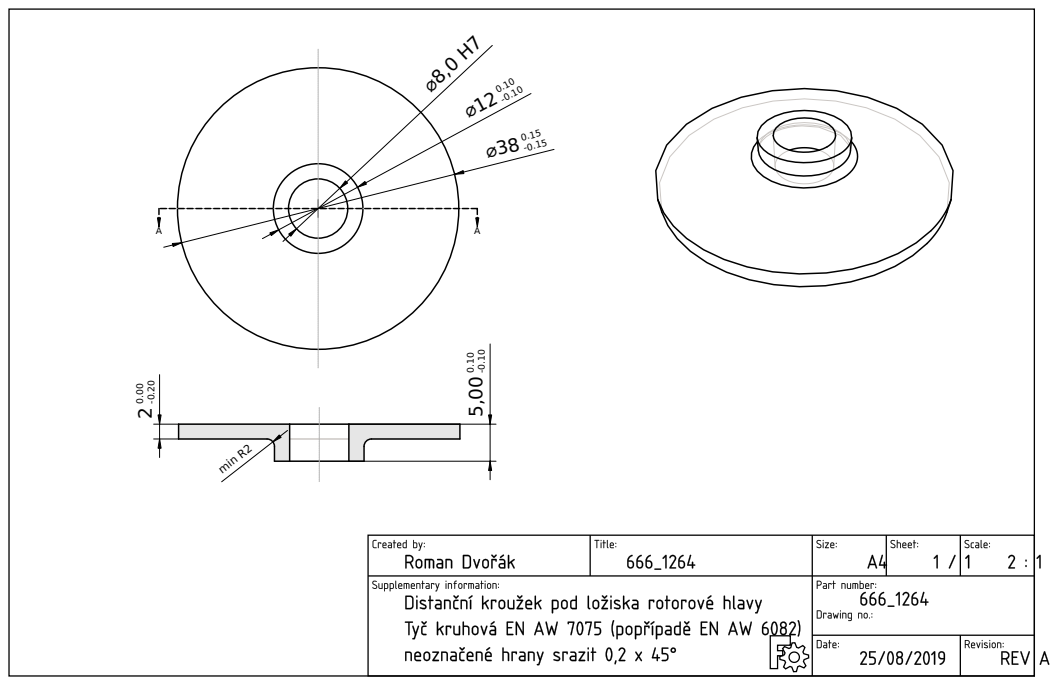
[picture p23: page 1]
min R2

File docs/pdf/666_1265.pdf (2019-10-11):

A⌀3

8,0

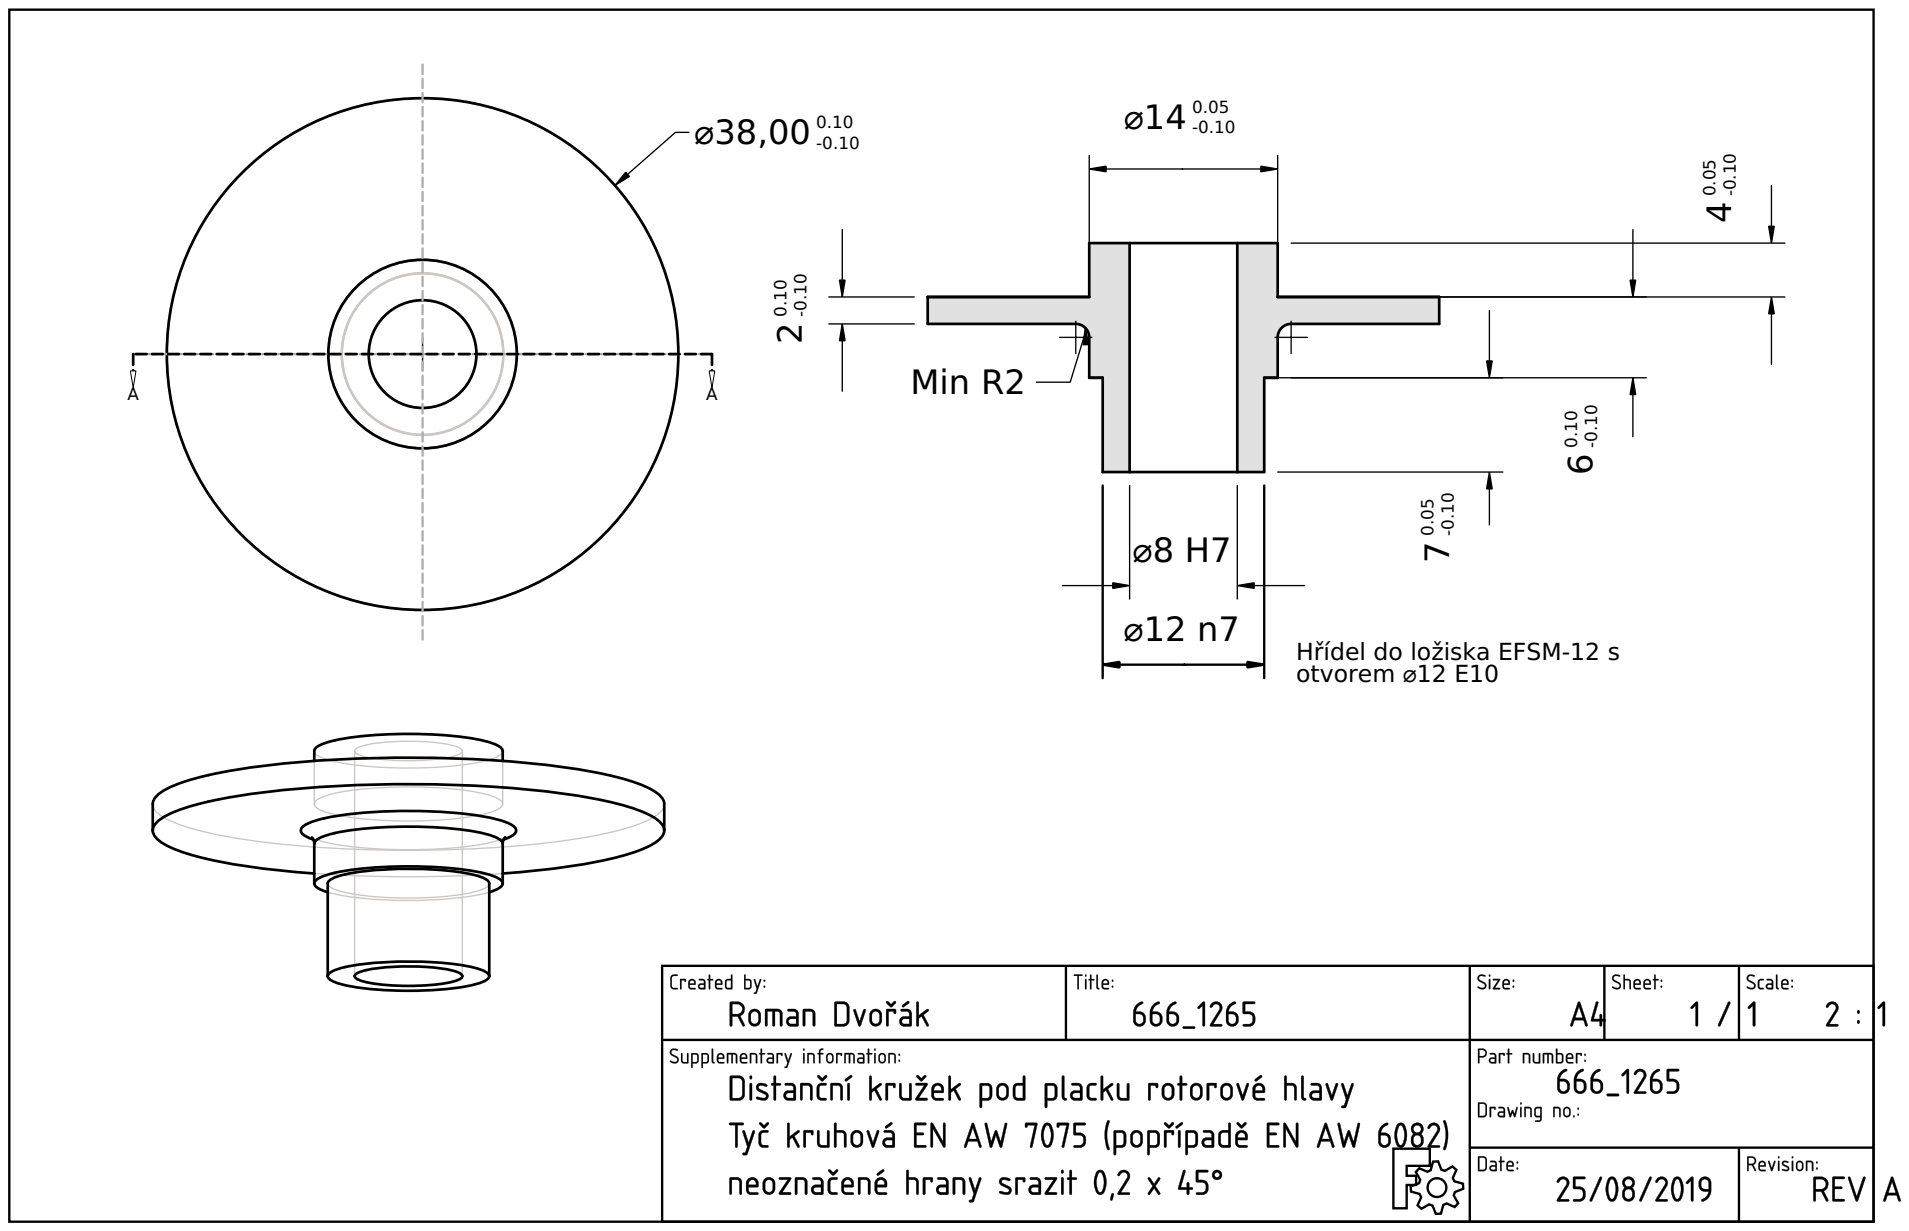
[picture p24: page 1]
Min; Hříd; žis; otv; ore

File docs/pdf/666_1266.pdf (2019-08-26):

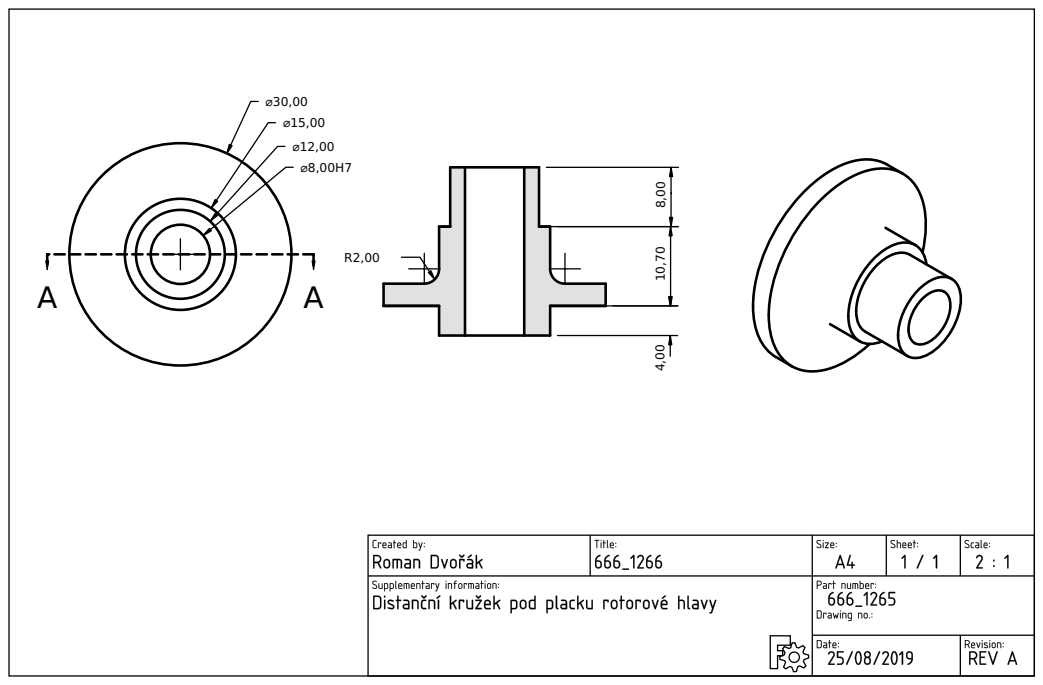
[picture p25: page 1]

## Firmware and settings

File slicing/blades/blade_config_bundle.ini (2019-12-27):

# generated by Slic3r 1.3.1-dev on Fri Dec 13 12:17:58 2019

[filament:3dlabprint_config01]
bed_temperature = 0
bridge_fan_speed = 100
compatible_printers = 
cooling = 0
disable_fan_first_layers = 3
end_filament_gcode = "; Filament-specific end gcode \n;END gcode for filament\n"
extrusion_multiplier = 1.02
fan_always_on = 0
fan_below_layer_time = 60
filament_colour = #FFFFFF
filament_cost = 0
filament_density = 0
filament_diameter = 1.75
filament_max_volumetric_speed = 0
filament_notes = ""
filament_settings_id = 
first_layer_bed_temperature = 0
first_layer_temperature = 215
max_fan_speed = 0
min_fan_speed = 0
min_print_speed = 10
slowdown_below_layer_time = 5
start_filament_gcode = "; Filament gcode\n"
temperature = 215

[filament:My Settings]
bed_temperature = 0
bridge_fan_speed = 100
compatible_printers = 
cooling = 1
disable_fan_first_layers = 3
end_filament_gcode = "; Filament-specific end gcode \n;END gcode for filament\n"
extrusion_multiplier = 1
fan_always_on = 0
fan_below_layer_time = 60
filament_colour = #FFFFFF
filament_cost = 0
filament_density = 0
filament_diameter = 1.75
filament_max_volumetric_speed = 0
filament_notes = ""
filament_settings_id = 
first_layer_bed_temperature = 0
first_layer_temperature = 205
max_fan_speed = 100
min_fan_speed = 35
min_print_speed = 10
slowdown_below_layer_time = 5
start_filament_gcode = "; Filament gcode\n"
temperature = 200

[filament:basic_part]
bed_temperature = 0
bridge_fan_speed = 100
compatible_printers = 
cooling = 1
disable_fan_first_layers = 2
end_filament_gcode = "; Filament-specific end gcode \n;END gcode for filament\n"
extrusion_multiplier = 1
fan_always_on = 0
fan_below_layer_time = 60
filament_colour = #FFFFFF
filament_cost = 0
filament_density = 0
filament_diameter = 1.75
filament_max_volumetric_speed = 0
filament_notes = ""
filament_settings_id = 
first_layer_bed_temperature = 0
first_layer_temperature = 215
max_fan_speed = 100
min_fan_speed = 35
min_print_speed = 10
slowdown_below_layer_time = 5
start_filament_gcode = "; Filament gcode\n"
temperature = 215

[presets]
filament = blade_2p.ini
print = blade_2p.ini
printer = blade_2p.ini

[print:3dlabprint_config01]
adaptive_slicing = 0
adaptive_slicing_quality = 75%
avoid_crossing_perimeters = 1
bottom_infill_pattern = rectilinear
bottom_solid_layers = 6
bridge_acceleration = 0
bridge_flow_ratio = 1
bridge_speed = 60
brim_connections_width = 0
brim_ears = 0
brim_ears_max_angle = 125
brim_width = 0
compatible_printers = 
complete_objects = 0
default_acceleration = 0
dont_support_bridges = 1
external_perimeter_extrusion_width = 0
external_perimeter_speed = 75%
external_perimeters_first = 0
extra_perimeters = 0
extruder_clearance_height = 20
extruder_clearance_radius = 20
extrusion_width = 0.41
fill_angle = 45
fill_density = 0%
fill_gaps = 1
fill_pattern = honeycomb
first_layer_acceleration = 0
first_layer_extrusion_width = 150%
first_layer_height = 0.2
first_layer_speed = 30
gap_fill_speed = 20
gcode_comments = 0
infill_acceleration = 0
infill_every_layers = 1
infill_extruder = 1
infill_extrusion_width = 0
infill_first = 0
infill_only_where_needed = 0
infill_overlap = 0%
infill_speed = 80
interface_shells = 0
interior_brim_width = 0
label_printed_objects = 0
layer_height = 0.2
match_horizontal_surfaces = 0
max_print_speed = 80
max_volumetric_speed = 0
min_shell_thickness = 0
min_skirt_length = 0
min_top_bottom_shell_thickness = 0
notes = 
only_retract_when_crossing_perimeters = 1
ooze_prevention = 0
output_filename_format = [input_filename_base].gcode
overhangs = 1
perimeter_acceleration = 0
perimeter_extruder = 1
perimeter_extrusion_width = 0
perimeter_speed = 60
perimeters = 2
post_process = 
print_settings_id = 
raft_layers = 0
regions_overlap = 0
resolution = 0
seam_position = random
shortcuts = support_material
skirt_distance = 1.5
skirt_height = 1
skirts = 2
small_perimeter_speed = 15
solid_infill_below_area = 70
solid_infill_every_layers = 0
solid_infill_extruder = 1
solid_infill_extrusion_width = 0
solid_infill_speed = 20
spiral_vase = 0
standby_temperature_delta = -5
support_material = 0
support_material_angle = 0
support_material_buildplate_only = 0
support_material_contact_distance = 0.2
support_material_enforce_layers = 0
support_material_extruder = 1
support_material_extrusion_width = 0
support_material_interface_extruder = 1
support_material_interface_extrusion_width = 0
support_material_interface_layers = 3
support_material_interface_spacing = 0
support_material_interface_speed = 100%
support_material_max_layers = 0
support_material_pattern = pillars
support_material_pillar_size = 2.5
support_material_pillar_spacing = 10
support_material_spacing = 2.5
support_material_speed = 60
support_material_threshold = 0
thin_walls = 1
top_infill_extrusion_width = 0
top_infill_pattern = rectilinear
top_solid_infill_speed = 15
top_solid_layers = 6
travel_speed = 150
xy_size_compensation = 0

[print:My Settings]
adaptive_slicing = 0
adaptive_slicing_quality = 75%
avoid_crossing_perimeters = 0
bottom_infill_pattern = rectilinear
bottom_solid_layers = 6
bridge_acceleration = 0
bridge_flow_ratio = 1
bridge_speed = 40
brim_connections_width = 0
brim_ears = 0
brim_ears_max_angle = 125
brim_width = 0
compatible_printers = 
complete_objects = 0
default_acceleration = 0
dont_support_bridges = 1
external_perimeter_extrusion_width = 0
external_perimeter_speed = 90%
external_perimeters_first = 0
extra_perimeters = 1
extruder_clearance_height = 20
extruder_clearance_radius = 20
extrusion_width = 0
fill_angle = 45
fill_density = 8%
fill_gaps = 1
fill_pattern = stars
first_layer_acceleration = 0
first_layer_extrusion_width = 200%
first_layer_height = 90%
first_layer_speed = 30
gap_fill_speed = 20
gcode_comments = 0
infill_acceleration = 0
infill_every_layers = 1
infill_extruder = 1
infill_extrusion_width = 0
infill_first = 0
infill_only_where_needed = 0
infill_overlap = 55%
infill_speed = 40
interface_shells = 0
interior_brim_width = 0
label_printed_objects = 0
layer_height = 0.1
match_horizontal_surfaces = 0
max_print_speed = 80
max_volumetric_speed = 0
min_shell_thickness = 0
min_skirt_length = 0
min_top_bottom_shell_thickness = 0
notes = 
only_retract_when_crossing_perimeters = 1
ooze_prevention = 0
output_filename_format = [input_filename_base].gcode
overhangs = 1
perimeter_acceleration = 0
perimeter_extruder = 1
perimeter_extrusion_width = 0
perimeter_speed = 40
perimeters = 3
post_process = 
print_settings_id = 
raft_layers = 0
regions_overlap = 0
resolution = 0
seam_position = aligned
shortcuts = support_material
skirt_distance = 6
skirt_height = 1
skirts = 1
small_perimeter_speed = 30
solid_infill_below_area = 70
solid_infill_every_layers = 0
solid_infill_extruder = 1
solid_infill_extrusion_width = 0
solid_infill_speed = 30
spiral_vase = 0
standby_temperature_delta = -5
support_material = 0
support_material_angle = 0
support_material_buildplate_only = 0
support_material_contact_distance = 0.2
support_material_enforce_layers = 0
support_material_extruder = 1
support_material_extrusion_width = 0
support_material_interface_extruder = 1
support_material_interface_extrusion_width = 0
support_material_interface_layers = 3
support_material_interface_spacing = 0
support_material_interface_speed = 100%
support_material_max_layers = 0
support_material_pattern = pillars
support_material_pillar_size = 2.5
support_material_pillar_spacing = 10
support_material_spacing = 2.5
support_material_speed = 40
support_material_threshold = 60%
thin_walls = 1
top_infill_extrusion_width = 0
top_infill_pattern = rectilinear
top_solid_infill_speed = 20
top_solid_layers = 6
travel_speed = 130
xy_size_compensation = 0
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

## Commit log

2018-05-21 zvětšila jsem šířku dílu z naca = 0005 na naca = 0010 a zapustila jsem servo v celé jeho výšce.
    [888_1010.scad]
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2018-05-23 Vložen nový parametr "Screw_head_height_M3" pro určení výšky hlavičky šroubu a pak vložen parametr "basic_screw_length" pro určení v jak velkém odstupu jsou k dispozici délky šroubů.
    [Parameters.scad]
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2018-05-23 Opravena spojka 666_1026.scad, tak aby bylo možné použít normalizované délky šroubů. Jelikož hlavička i matka jsou zvenku spojky, tak šířka spojky, je zmenšena o výšku hlavičky šroubu,aby šroub přečn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
    [666_1026.scad]
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2018-05-28 Posunutí akumulátorů, posunutí otvoru pro spojku 666_1017 v podložce. Posunutí dělení podložky.
    [666_1027.scad, Parameters.scad]
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2018-05-29 Vytvoření otvorů pro uchycení serva a směrovky. Zaveden nový parametr pro průměr čepy pro uchycení směrovky.
    [666_1028.scad, 888_1010.scad, 888_1012.scad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]
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2018-05-30 Zrušení commitů následujících po revizi 8e367852ed3c9e9abf32f666672e102ae146ea34 Zjistil jsem, že tyto commity nepřinesly žádné užitečné úpravy, ale došlo ke smazání významného množství dat.
    [666_1028.scad, 666_1038.dxf, 666_1201.scad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]
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2018-05-30 Rozšíření předního plastového dílu pro držák motoru. FIXED: #131
    [888_1026.scad, print_plate_1026_engine.scad, print_plate_1026_engine.stl]
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2018-06-04 Revert "Zkrácení šroubů pro připevnění podložky k hlavní trubce."
    [666_1027.scad, Parameters.scad, print_plate_1027.stl]
2018-06-04 Oprava přípravku pro ohyb 2 a 3 - po změně parametrů byla krátká dlouhá rovná hrana.
    Oprava přípavků pro ohyb 1 a 4 - otočení o 90°pro opření o stěnu.
    [888_1013.scad]
2018-06-04 Revert "Revert "Zkrácení šroubů pro připevnění podložky k hlavní trubce.""
    [666_1027.scad, Parameters.scad, print_plate_1027.stl]
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2018-06-07 Úprava pohyblivé části směrovky pro přímou montáž koupené páky.
    Přegenerování modelů pro tisk.
    [666_1028.scad, print_plate_1028_rudder.stl, print_plate_1028_servo.stl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]
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2018-06-07 Opravení chyby ve výpočtu tloušťky bloku pro páku. Posunutí páky více dozadu.
    [666_1028.scad, print_plate_1028_rudder.stl]
2018-06-11 Doplnění zbylých dvou úhlopříčných děr, aby bylo možné použít na stejné místo levou i pravou páku s kulovým ložiskem MPJ 2231.
    [666_1028.scad]
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2018-06-13 Rozšíření předního dílu pro servo snížení styčné plochy s podložkou u ocasních ploch.
    [666_1028.scad, 888_1010.stl, 888_1026.scad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]
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2018-06-13 Kostka se šrouby pousnuta na spodní stranu. Trubka zapuštěna tak, aby nepřečnívala.
    [888_1013.scad]
2018-06-13 Úprava výklenku pro servo. - dočasná deaktivace integrovaného rámečku. - Vytvoření provizorních prostupů pro kabely serva - Přidány plochy pro lepší adhezi k tiskové podložce během tisku.
    [666_1028.scad, print_plate_1028.scad, print_plate_1028.stl]
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2018-06-21 Otvory pro připevnění spojky na hlavní trubky experimentálně změněny na M4 kvůli otestování lepší pevnosti.
    [666_1017.scad, print_plate_1017.stl]
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2018-06-28 Rozšíření spojky 1017 pro lepší pevnost.
    Přegenerování modelů a jejich aktualizace pro simulátor.
    [666_1017.scad, 666_1026.stl, 666_1027.scad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]
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2018-07-05 Zavedení globálního parametru pro nastavení úhlu náběhu listů. A vygenerování nových podložek.
    [666_1004.stl, 666_1247.scad, 666_1247.stl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]
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2018-07-18 Přidání prostupu pro přívody motoru do přední části krytu a vygenerování nových tiskových dat.
    [666_1025.scad, print_plate_1025A.stl, print_plate_1025E.stl]
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2018-08-17 Rozšíření držáku pro servo na zadním kolečku, aby do něj bylo možné uchytit i velké servo.
    [888_2001.scad, print_plate_2001.scad, print_plate_2001.stl]
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2018-08-22 Nový vrtací přípravek pro díl 666_1004 FIXED: #144
    [666_1004.scad, 888_1011.stl, 888_1013.stl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]
2018-08-22 Vytvoření přípravku na řezání trubek. FIXED: #145
    [tube_cutter.scad, tube_cutter.stl]
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2018-09-07 Zmenšená tolerance otvorů pro magnety.
    [rotor_pulley.scad]
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2018-09-11 Opravení vrtacího přípravku - umístění druhého šroubu pro připevnění k podvozkové trubce.
    [666_1014.scad]
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2018-09-12 Oprava velkých písmen v názvu na malá tak, aby to bylo stejné jako u ostatních souborů.
    [screw_cutter.scad]
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2018-09-18 Upraven návrh ostruhového kolečka tak, aby mělo menší vůle. Přidán nový díl s kuličkovými ložisky.
    [888_2002.scad, 888_2003.stl, 888_2004.scad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]
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2018-09-18 Nový díl - první díl z issue 156
    [888_3000.scad]
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2018-09-18 Zobrazení podložky pro názornost otvoru prvního šroubu pro připevnění k horizontální trubce.
    [888_1014.scad]
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2018-09-18 Nový díl - dle issue 156 - druhý díl
    [888_3001.scad]
2018-09-19 Přesunutí ložisek do pohyblivé části příďového kola, kvůli lepší montáži a vyšší pevnosti.
    [666_1038.stl, 888_2002.scad, 888_2002.stl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]
2018-09-19 Zdvojení sřoubů ve vložkách pro tenčí trubky podvozkových ližin v příčných trubkách.
    [666_1006.scad, 666_1006.stl, print_plate_1006.stl]
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2018-09-19 Opraveny parametry, doplněny sloupky s otvorem pro šroub a kapsou pro matku.
    [888_3000.scad]
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2018-09-19 Nový díl 888_3002.scad - třetí díl z issue 156. Nový díl 888_3003.scad - sestava
    [888_3002.scad, 888_3003.scad]
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2018-09-20 presun loziska z dilu 3001 do dilu 3002, odstraneni zapusti pro lozisko z dilu 3002 na osu k 3003
    [888_3001.scad, 888_3002.scad]
2018-09-20 zmenseni dilu 3001, 3002; podlozka pod prvni licovany sroub v dilu 3001
    [888_3001.scad, 888_3002.scad, 888_3003.scad]
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2018-09-20 888_3003.scad - díl 4. + 5. dle issue 156 888_3004.scad - díl 6. dle issue 156 888_3005.scad - díl 7. dle issue 156
    [888_3003.scad, 888_3004.scad, 888_3005.scad]
2018-09-20 Modifikace dle požadavků v issue 156
    [888_3003.scad, 888_3004.scad, 888_3005.scad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]
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2018-09-21 Zvětšení tolerance otvoru pro ložisko.
    [888_3000.stl, 888_3003.stl, Parameters.scad]
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2018-09-25 novy dil 888_3007 pro pridelani na strechu auta a uprava 888_3006 - zakladna na strechu auta
    [888_3006.scad, 888_3102.scad, Parameters.scad]
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2018-09-26 Doplění otvorů pro šrouby a matky M2.5; Změna pozice otvoru pro čep; Rozšíření otvoru pro ložisko; Posunutí otvoru pro servo;
    [888_1015.scad]
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2018-09-26 do dilu 888_3006 pridan u zakladny valec pro lepsi tisk, novy dil 888_3009 - podlozka pod zakladnu na auto
    [888_3006.scad, 888_3009.scad, Parameters.scad]
2018-09-26 Posunutí výřezu na čep proti otáčení do správné vzdálenosti od osy kulového čepu.
    [888_1015.scad]
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2018-11-20 Zkosení dle issue 130.
    [666_1028.scad]
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2018-12-05 hall wide hole fix
    [888_1020.scad]
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2018-12-12 FIX #164 Nastavení délky otvorů pro upevnění šrouby M4x45.
    [888_1015.scad, print_plate_888_1015.stl]
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2019-05-01 Fix white symbol on the first row of parameters.scad file.
    [333_1037.stl, 666_1232.stl, 888_1018.stl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]
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2019-05-07 Fix code miscopy.
    [888_3007.scad]
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2019-05-16 fix parameter supplied more than once.
    [888_3006.scad]
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2019-06-10 fix #187 vypouštěcí zařízení
    [888_1026.scad, Parameters.scad]
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2019-06-13 FIX #192
    Magnet musel být trochu vyosen oproti původnímu držáku, kvůli udržení způsobu montáže šroubů a jejich rozteče.
    [888_1015.stl, 888_1026.stl, 888_1027.stl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]
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2019-06-14 bug fix, je potřeba doplnit správné hodnoty k parametrům DS313MG_XX
    [888_1026.scad, Parameters.scad]
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2019-06-18 Fix relative paths.
    [carbon.scad, pla.scad]
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2019-07-04 resolved #117
    [888_2014.scad, 888_2015.scad]
2019-07-04 Kompletní přepracování dílu, zmenseni rozmeru, render
    Resolved: #204
    [888_2013.scad, 888_2013.stl]
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2019-07-22 Resolved: #206 optimalizace hmotnosti + render
    [888_2016.scad, parameters.scad, print_plate_888_2016.stl]
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2019-08-23 Rudder shaped as A new code
    still missing pipe piece
    [666_1028.scad, parameters.scad]
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2019-09-12 Rudder after print issues repair #194
    [666_1028.scad]
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2019-09-27 Rudder temporary height fix #194
    [666_1028.scad, parameters.scad]
2019-09-27 Rudder wire guide fix #194
    [666_1028.scad]
2019-09-27 Rudder bottom ribs fix #194
    [666_1028.scad]
2019-09-27 Rudder moving part size fix #194
    [666_1028.scad]
2019-09-27 Rudder side_choose fix #194
    [666_1028.scad]
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2019-10-11 Revert "Merge remote-tracking branch 'refs/remotes/origin/improved_suspension'"
    This reverts commit ef15156073430ef0264117e8580aa23e4af52a13.
    [parameters.scad]
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2019-10-13 Rudder shaft dynamic fix #194
    [666_1028.scad]
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2019-10-16 Rudder mount screws fix #194
    [666_1028.scad]
2019-10-16 Rudder servo holes fix #194
    [666_1028.scad, parameters.scad]
2019-10-16 Rudder shaft end fix #194
    [666_1028.scad]
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2019-10-16 Rudder servo arm offset fix #194
    [666_1028.scad, parameters.scad]
2019-10-16 Rudder servo arm bug fix #194
    [666_1028.scad]
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2019-10-16 Rudder wire tunnel hole fix #194
    [666_1028.scad]
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2019-10-20 Rudder adapter print plate fix #194
    [print_plate_1028_adapter.scad]
2019-10-20 Rudder top part fix #194
    [666_1028.scad, parameters.scad]
2019-10-20 Rudder sharp edge fix #194
    [666_1028.scad, parameters.scad]
2019-10-20 Rudder gap fix #194
    [666_1028.scad, parameters.scad]
2019-10-20 Rudder moving part reverse infill #194
    [666_1028.scad]
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2019-10-21 FIX #194
    Přidání oblého tvaru na spodní stranu směrovky.
    [666_1028.scad, 666_1201.scad, print_plate_1028_body_bottom_left.scad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]
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2019-10-21 Resolved #254
    [888_1020.scad, print_plate_1020.scad, print_plate_1020.stl]
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2019-10-22 Rudder adapter holes and edge fix #194
    [666_1028.scad]
2019-10-22 Rudder servo hole dimesions fix #194
    [666_1028.scad, parameters.scad]
2019-10-22 Rudder servo hole fix #194
    [666_1028.scad]
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2019-10-22 Rudder wire tunnel fix #194
    [666_1028.scad, parameters.scad]
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2019-10-22 Rudder servo center fix #194
    [parameters.scad]
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2019-10-23 Rudder minor fixs #194
    [666_1028.scad, parameters.scad]
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2019-10-30 Rudder adapter clearance fix #194
    [666_1028.scad]
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2019-11-12 Rudder washer bug fix #266
    [666_1028.scad]
2019-11-12 Rudder bug fix #266
    [666_1028.scad]
2019-11-12 Rudder fixing made bugs
    [666_1028.scad]
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2019-11-13 Rudder washer fix & servo arm symetric #266
    [666_1028.scad]
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2019-11-14 orientate fixed
    [888_2024.scad]
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2020-01-23 Rudder inverted code half way done #271
    [666_1028.scad]
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2020-01-26 Rudder tube mount reversed model done #271
    [666_1028.scad]
2020-01-26 Rudder top part reverse model done #271
    [666_1028.scad, parameters.scad]
2020-01-29 Rudder passive rudder reverse model done #271
    [666_1028.scad]
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2020-02-05 Rudder moving part reverse model done #271
    [666_1028.scad, parameters.scad]
2020-02-10 Rudder all parts reversed #271
    [666_1028.scad, parameters.scad]
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2020-02-19 FIX WARNING: argument rotate supplied more than once, in file print_plate_888_2013.scad, line 8
    [print_plate_888_2013.scad]
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2020-02-28 Increase spacing between moving parts.
    FIX #282
    [888_2025.scad, parameters.scad, print_plate_888_2025.amf]
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2020-06-22 Fix #286
    Pozice zapusteni pro hlavy šroubů zvýšena nad spodní šroub uchycení zadní nohy pylonu.
    [888_1030.scad, print_plate_888_1030.amf]
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2020-07-20 Holes num of polygons fix
    [888_1037.scad]
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2020-07-27 Bug fix #288
    [888_1037.scad]
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
